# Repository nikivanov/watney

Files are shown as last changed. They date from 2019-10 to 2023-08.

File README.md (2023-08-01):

# Watney Rover
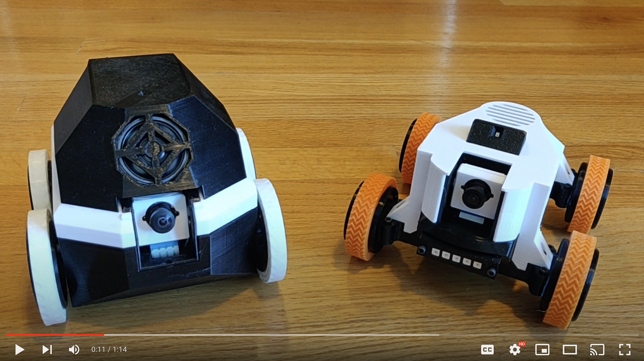
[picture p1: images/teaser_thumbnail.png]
(https://www.youtube.com/watch?v=ayU9SmKKkow)

Watney is an open source, Raspberry Pi-enabled telepresence rover made of readily available parts.
Non-electronic parts of Watney are 3D printable.
Watney provides a low-latency HD video feed as well as bi-directional audio with echo cancellation.
Watney uses a charging dock with passthrough charging for continuous operation.

If you've enjoyed this project and want to buy me a beer (no pressure): 

# Components
Head over to [Bill of Materials](BOM.md) for a list of components you need to purchase to build your own Watney. You'll also need a 3D printer, some PETG / Tough PLA as well as TPU filament. Lastly, you'll need a soldering iron and some wires, though most connections are made using standard breadboard jumper wire.

# UPS Firmware Update
Before you start assembling your Watney, be sure to update the firmware of the UPS power supply. At the time of writing, the latest firmware is *v10* - all previous firmware versions suffered from occasional lockups. You can find [firmware update instructions here.](https://wiki.52pi.com/index.php/EP-0136#Method_2)

# Printing the parts
You can find all 3D printable parts in the [STLs folder](https://github.com/nikivanov/watney/tree/master/STLs). I recommend printing everything but the tires in PETG (I used eSun PETG) or at least Tough PLA. I find regular PLA to be too brittle but YMMV. Print the tires in TPU - Hatchbox TPU worked great for me, but others will almost certainly work just as well.

Print every part with 0.2mm layer height. No supports are needed. The base part includes tearaway lilypads to help with adhesion. Generally, the prints can take a long time but none of them are particularly challenging to print.

# Assembly
You'll be working with Lithium Ion batteries - please be careful not to puncture or short them, as they can become a fire hazard if used improperly. **You assume all responsibility for damages that may be caused by your Watney, whether it's assembled correctly or otherwise.**

Click on the [Releases](https://github.com/nikivanov/watney/releases) tab and download the [latest Watney SD card image](https://github.com/nikivanov/watney/releases/latest) - it's the large .zip file found under *Assets*. Use [balenaEtcher](https://www.balena.io/etcher/) or similar to write the .img file onto the SD card.

After that, follow the detailed assembly video below!

Wiring diagrams that you see in the video can also be [found here](https://github.com/nikivanov/watney/tree/master/images/wiring).

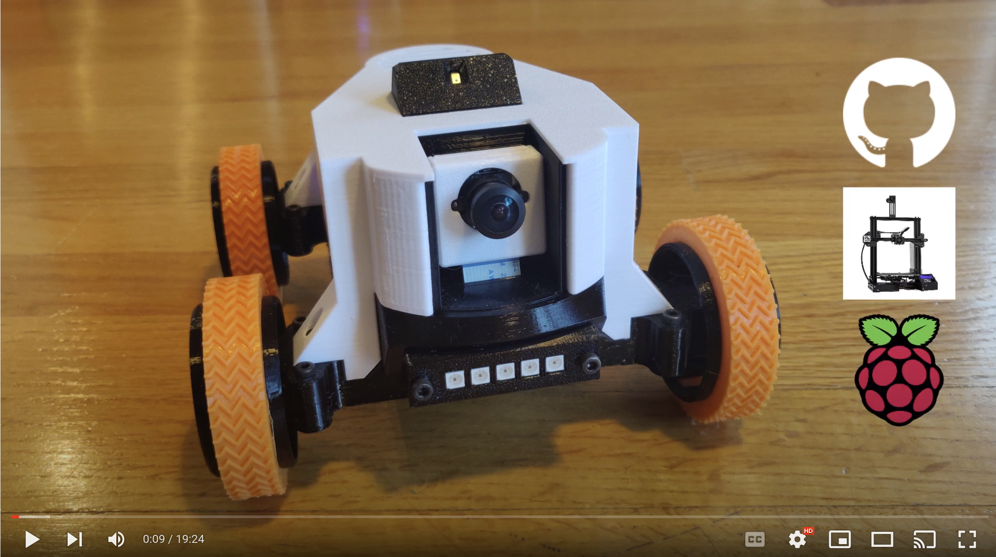
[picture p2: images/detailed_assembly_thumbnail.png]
(https://www.youtube.com/watch?v=wV26r6FtXRw)

 
# Configuration
Upon startup, Watney will detect if it's connected to a Wi-Fi hotspot. If not, it will host its own hotspot "Watney".
Once you connect to the hotspot, you can control it directly by going to https://192.168.4.1:5000, or connect it to a Wi-Fi
hotspot by going to http://192.168.4.1 Once you specify your WiFi credentials, Watney will take some time to reboot. Once you hear the startup sound, you're good to go!

Default SSH credentials for Watney are pi / watney5. Watney's mDNS name is watney.local, so if your OS supports mDNS you can simply access it at https://watney.local:5000

Watney's configuration can be found in ~/watney/rover.conf:
* If you want to use different GPIO pins, you can specify them here
* If you find motors on either side running in reverse (backwards when it's supposed to be rotating forward) simply swap ForwardPin 
and ReversePin
* Restart your Watney for configuration changes to take effect

    ## Off Charger re-docking
    Watney can detect when it is taken off the charger outside of its own movement and can attempt to re-dock by driving forward for one second. In my case, Watney occasionally gets knocked off the charger by my Roomba, so enabling this functionality ensures that Watney is always docked and charging. By default this functionality is disabled: I didn't want Watney to drive off someone's workbench while they are working on it. If you'd like to enable this functionality, set `Enabled=True` in the `OFFCHARGER` section of the config.
# Remote Access
Watney has no authentication / security. If you'd like to set it up for remote access, I recommend using [Zerotier](https://www.zerotier.com/). Adding Watney and your client computer to the same Zerotier network will make it appear as if they are on the same local network.

# Building your own Watney image
`packer-builder-arm` is used to build the Watney image. You can find the image build definition in [watney-image.json](packer/watney-image.json). [This article](https://linuxhit.com/build-a-raspberry-pi-image-packer-packer-builder-arm/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,server%20or%20other%20x86%20hardware.) may help setting up `packer` and `packer-builder-arm` on your linux system.

# Raspberry Pi Compatibility
Watney is designed to work with Raspberry Pi 3A+, however other versions may be compatible:
* [scifiguy000](https://github.com/scifiguy000) confirmed to have successfully used a Raspberry Pi 4B in [this thread](https://github.com/nikivanov/watney/issues/27)
* Raspberry Pi Zero 2 may work out of the box, but has not been confirmed yet

# Camera Module Compatibility
[camrichmond](https://github.com/camrichmond) discovered that the newest Raspberry Pi camera module v3 is not compatible with the current Watney image, since the camera module itself is not compatible with `raspivid`, which is how Watney gets
its hardware-encoded h264 video stream. New Bullseye RPi images use `libcamera` instead. The fix is to simply change the command in `video.sh` as detailed [in this comment](https://github.com/nikivanov/watney/issues/34#issuecomment-1646009610). Additionally, [camrichmond](https://github.com/camrichmond) modified the camera housing for the new camera module, which you can [download here](https://github.com/camrichmond/watney_Pi_CameraV3). Thanks [camrichmond](https://github.com/camrichmond)!

# Troubleshooting
* Watney works best with Chrome. Other browsers may not work well, or at all.
* Feel free to file an issue on GitHub if you have questions!

# Open Source Acknowledgements
The following open source projects were used in development of Watney:
* [Janus WebRTC Server](https://janus.conf.meetecho.com/)
* [GStreamer](https://gstreamer.freedesktop.org/)
* [Raspberry Pi Turnkey](https://github.com/schollz/raspberry-pi-turnkey) 

# Future Improvements
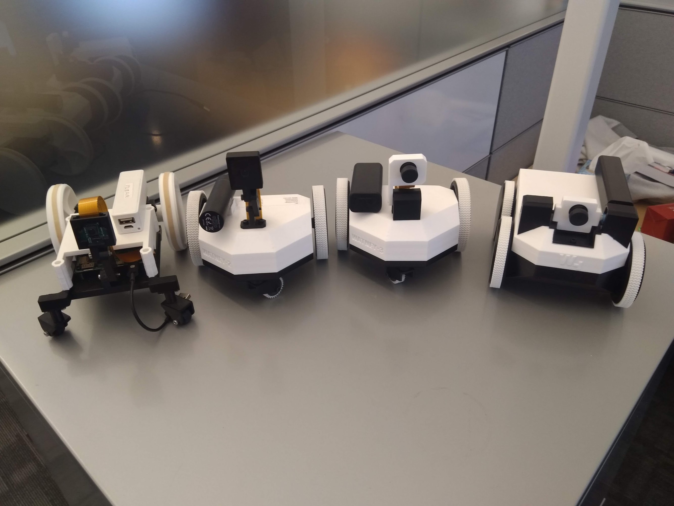
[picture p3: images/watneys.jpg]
Watneys

There have been numerous hardware iterations of Watney, starting from a humble line-follower built for a hackday work project, to the telepresence rover it is today. I'm not planning on adding new hardware iterations, as the latest version accomplishes everything I've envisioned for this project. That being said, there are still some software improvements to be made:
* **Mobile-optimized control.** You'll be able to control your watney from your phone / tablet, especially in tandem with Remote Access.
* **Better browser compatibility.** There's no reason it can't work in all major browsers.

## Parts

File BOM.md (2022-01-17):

# Bill of Materials
All parts can be found on Amazon, AliExpress, Ebay etc. Make sure the items you're ordering match the pictures. If you want to save money, order from AliExpress. Amazon will save you time on shipping, but will cost more. 

|Part| Reference Photo | Price | Notes |
|---|---|---|---|
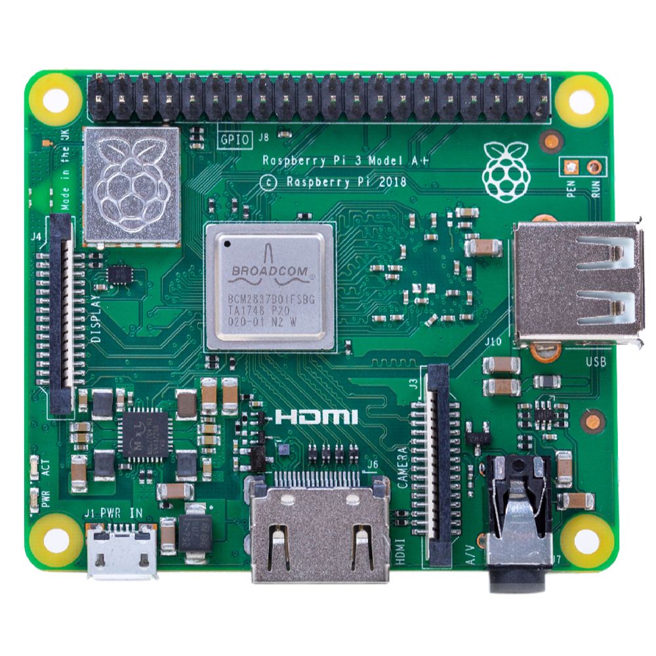
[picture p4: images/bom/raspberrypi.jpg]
raspberrypi
|Raspberry Pi 3A+|| $25 |
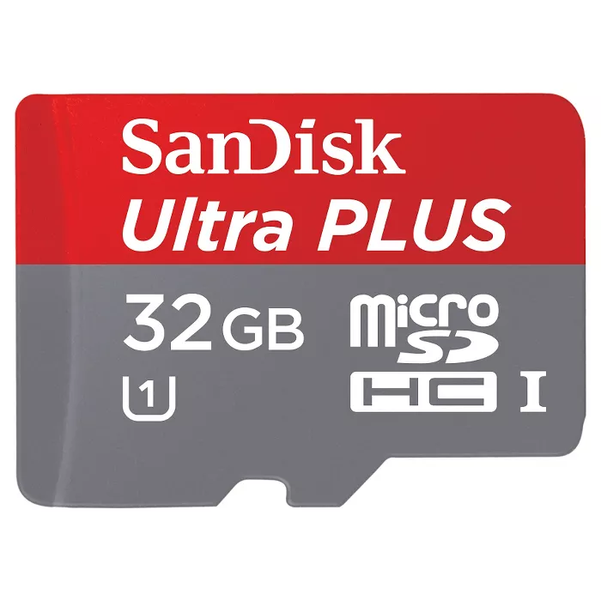
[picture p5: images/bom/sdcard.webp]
sdcard
| Micro SD Card 8GB+ | | $5 |
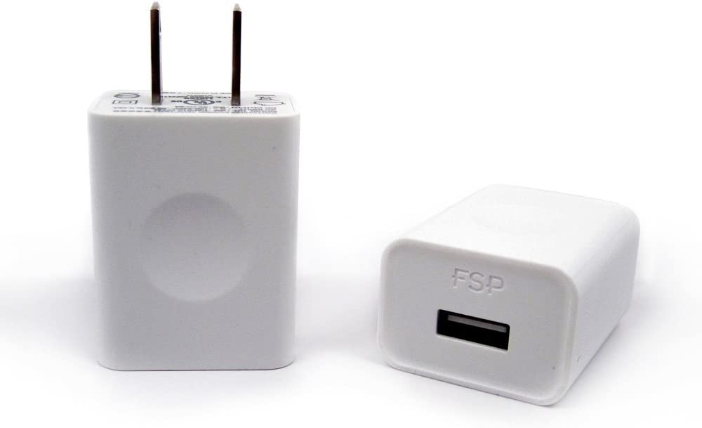
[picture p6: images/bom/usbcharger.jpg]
| 2A USB charger |  | $5 | 
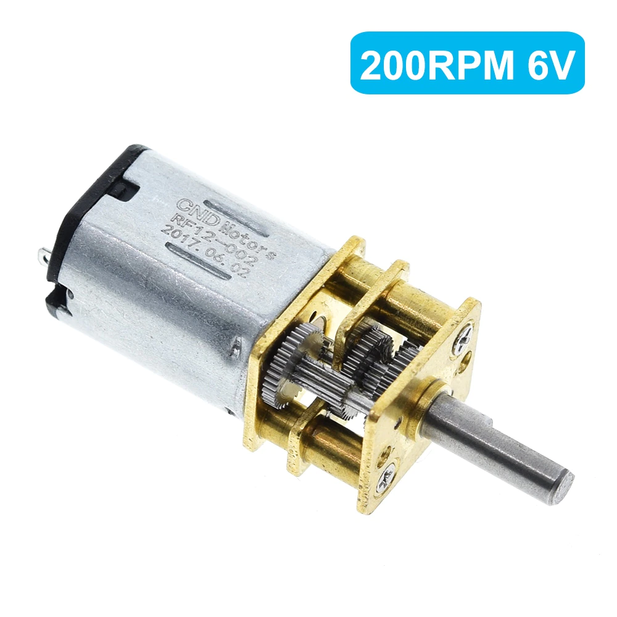
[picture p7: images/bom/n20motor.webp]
n20motor
| 4x N20 geared motors, 10mm shaft, 200 rpm, 6V | | $14 total | You can choose a lower speed to get more torque, but 200 rpm seems to have the best balance of torque to speed
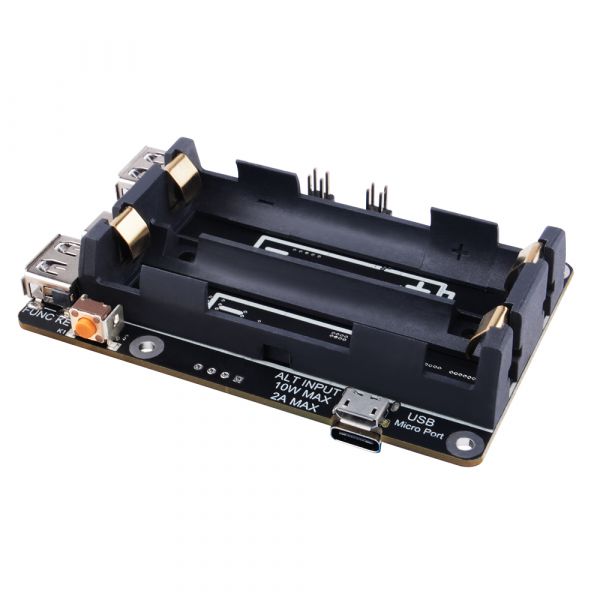
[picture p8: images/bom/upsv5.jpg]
upsv5
| GeeekPi UPS Plus V5 EP-0136  |  | $30 | Product Wiki: https://wiki.52pi.com/index.php/UPS_Plus_SKU:_EP-0136
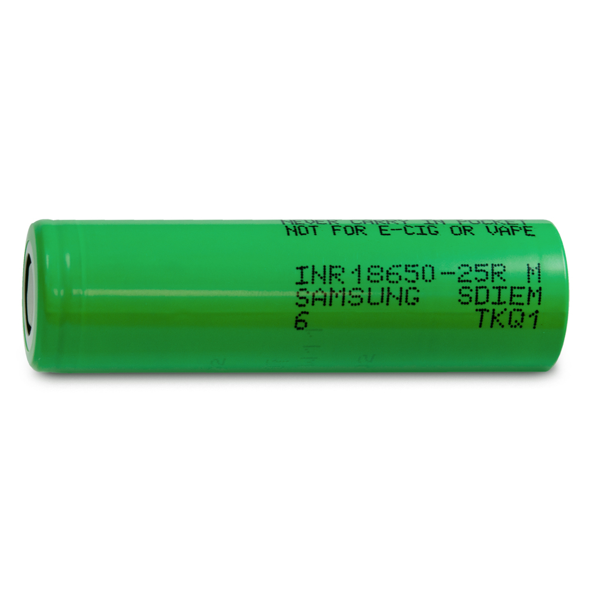
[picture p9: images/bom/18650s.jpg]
| 2x 18650 batteries | | $20 | The price is for 2 Samsung 25R batteries. You can save money by buying cheap 18650s with mixed results
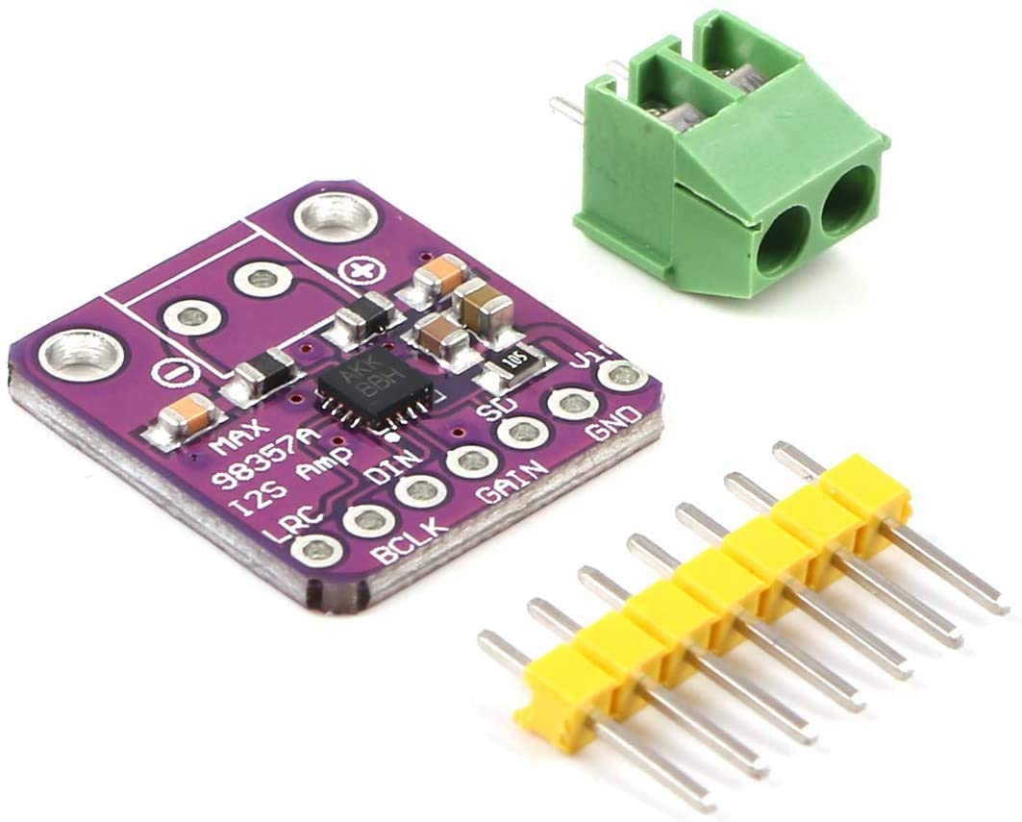
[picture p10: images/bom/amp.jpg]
amp
| MAX98357 I2S amplifier | | $4
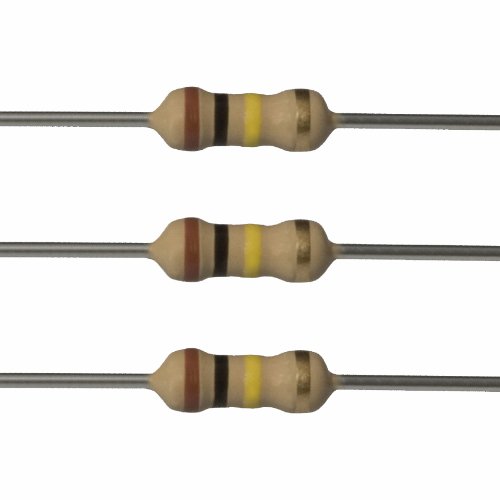
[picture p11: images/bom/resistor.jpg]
resistor
| 100k Ohm resistor | | $3 | Optional. Come in packs of 100 for the price 
| 40mm full range speaker |speaker | $5 | Usually come in packs of 2, but you only need one.
| Sipeed I2S microphone MSM261S4030H0 |microphone | $4 | Can be found under different names, but as long as it matches the image you should be good
| SG90 servo |servo | $4 | You may also be able to use the version with metal gears MG90. I haven't tried it but it should be a drop-in replacement
| Raspberry Pi fish eye camera | camera | $10
| DRV8833 motor driver |motordriver | $2
| 2.54mm 4 pin screw terminal |screwterminal | $3 | Usually come in pack of 10 for the price, but you only need 1
| SK9822 or APA102 144 LED/m strip |led | $20 | You only need a strip of 5 LEDs but the shortest strip you can get is 1 meter. You need the non-waterproof version, sometimes referred to as IP30
| 4x Keystone 209 contacts |keystone | $6
| Micro USB female breakout board |microusbfemale | $2 | This and the following USB boards usually come in a pack of 5 for the price
| 2x USB Type-A male breakout board |usbmale | $2 | 
| Micro USB male breakout plug |microusbmale | $2 | 
| 10cm and 20cm Female-to-Female Dupont jumper wire |  | $3
| M3 Bolt Hex Socket Round Cap 6mm 8mm 12mm 16mm 20mm |m3 | $6 
| 2.54m pitch male breakable pin header |header | $2 | You only need a few of these
| | | **Total**: ~$170 |

You'll also need general purpose hookup wire (in a pinch you can use jumper wire) and basic soldering equipment.

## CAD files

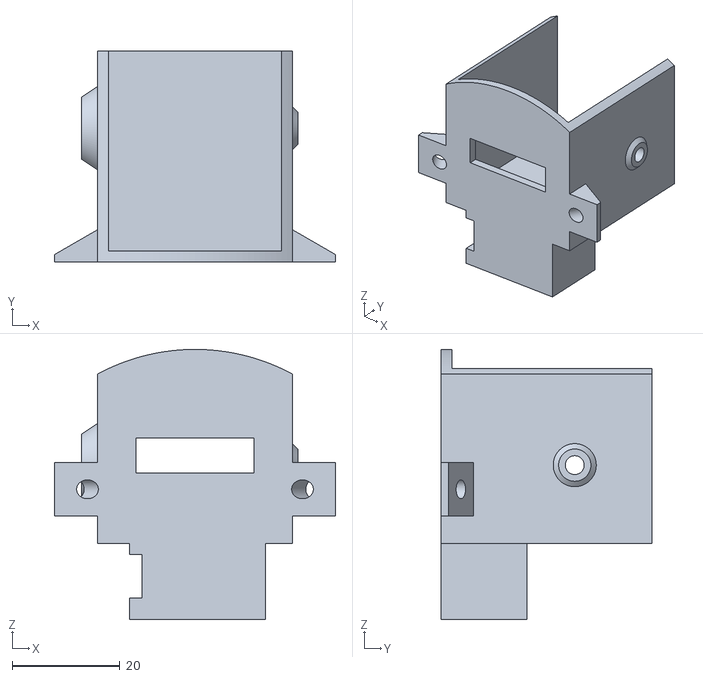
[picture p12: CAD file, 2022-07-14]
STLs/black parts/Camera bucket mg90s.stl
52.2 x 39.2 x 50.2

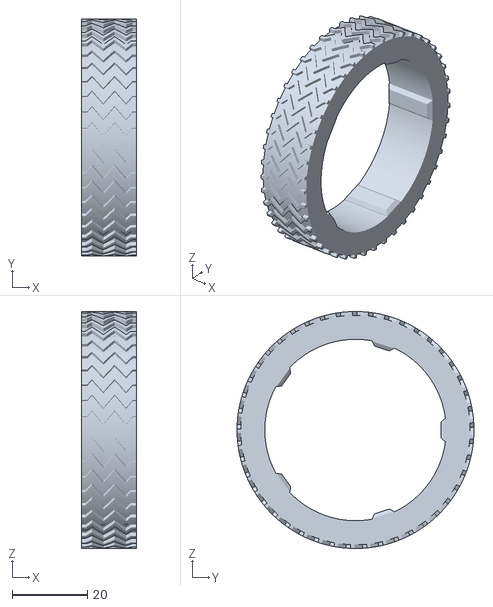
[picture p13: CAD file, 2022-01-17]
STLs/orange parts/tire.stl
14.5 x 63.0 x 63.0

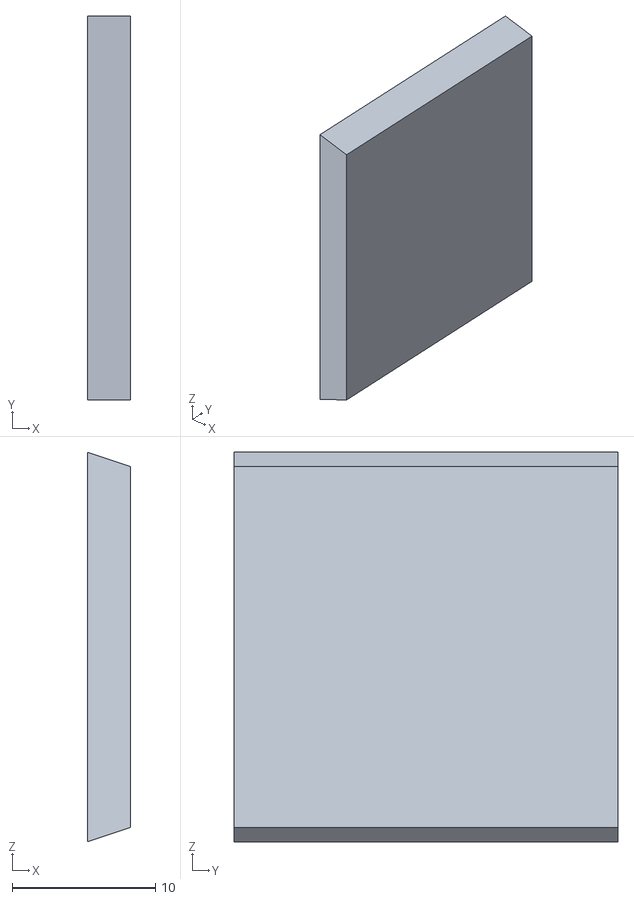
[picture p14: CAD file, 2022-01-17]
STLs/white parts/camera door.stl
3.00 x 26.8 x 27.2

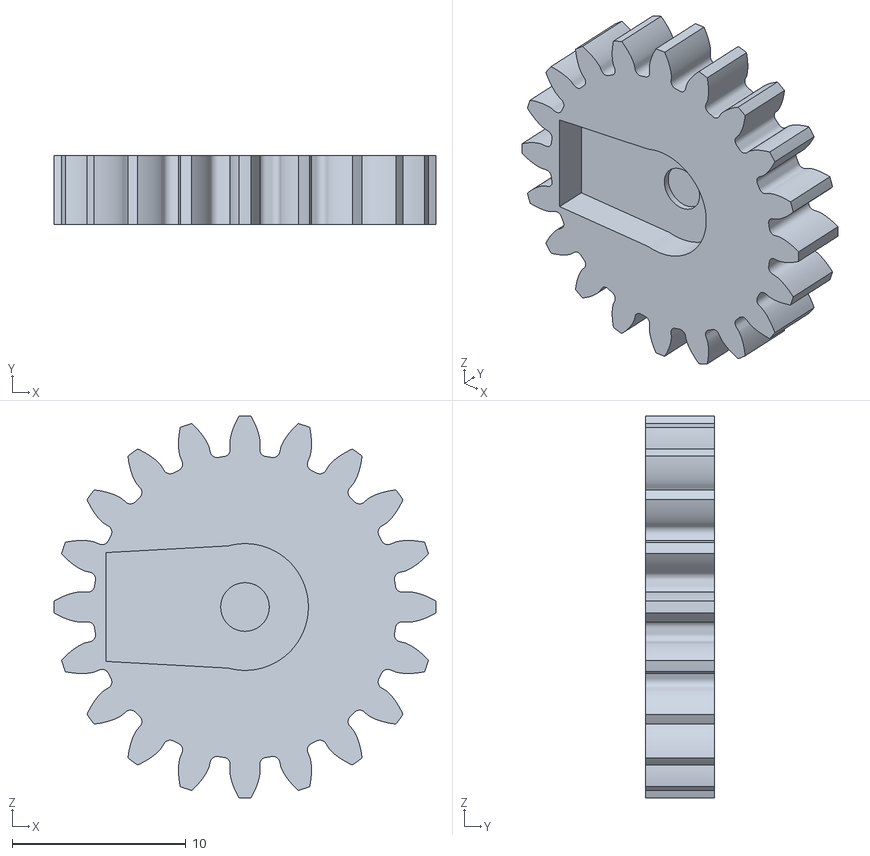
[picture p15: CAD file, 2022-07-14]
STLs/black parts/servo gear mg90s.stl
22.0 x 4.00 x 22.0

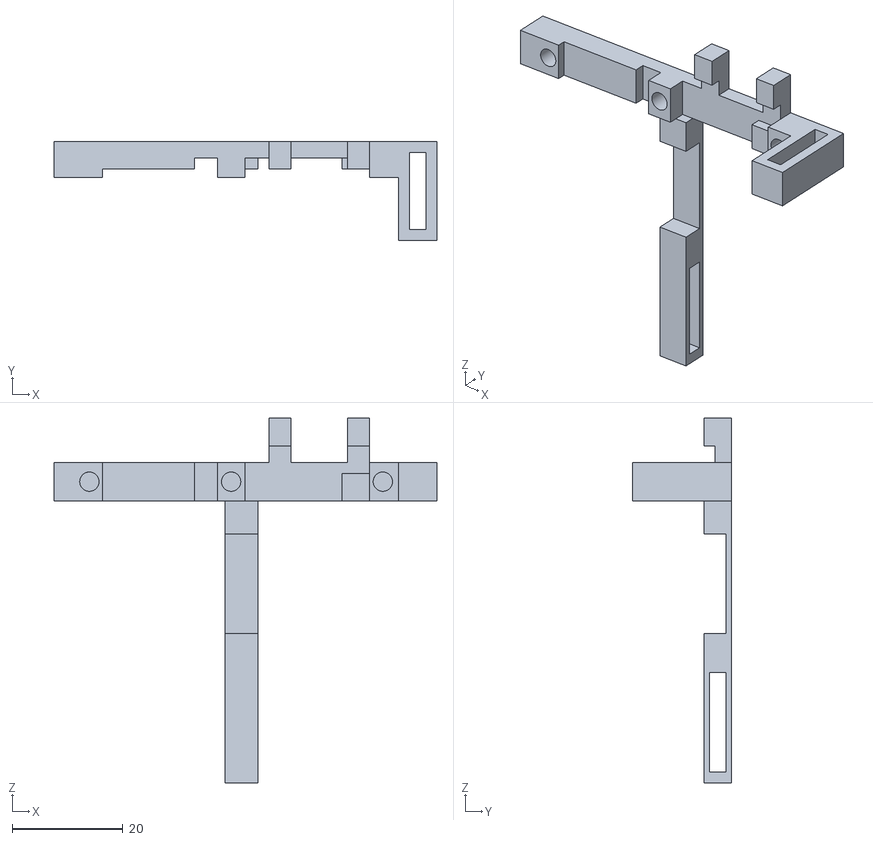
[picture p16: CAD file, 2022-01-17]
STLs/white parts/component clamp.stl
69.3 x 18.0 x 66.0

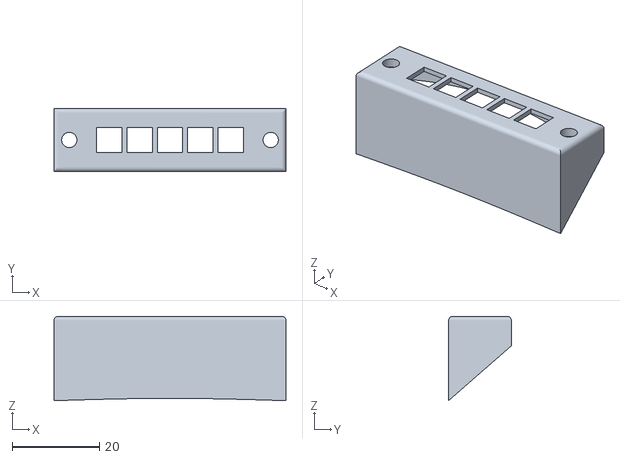
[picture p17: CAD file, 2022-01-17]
STLs/black parts/headlight case.stl
53.1 x 14.4 x 19.3

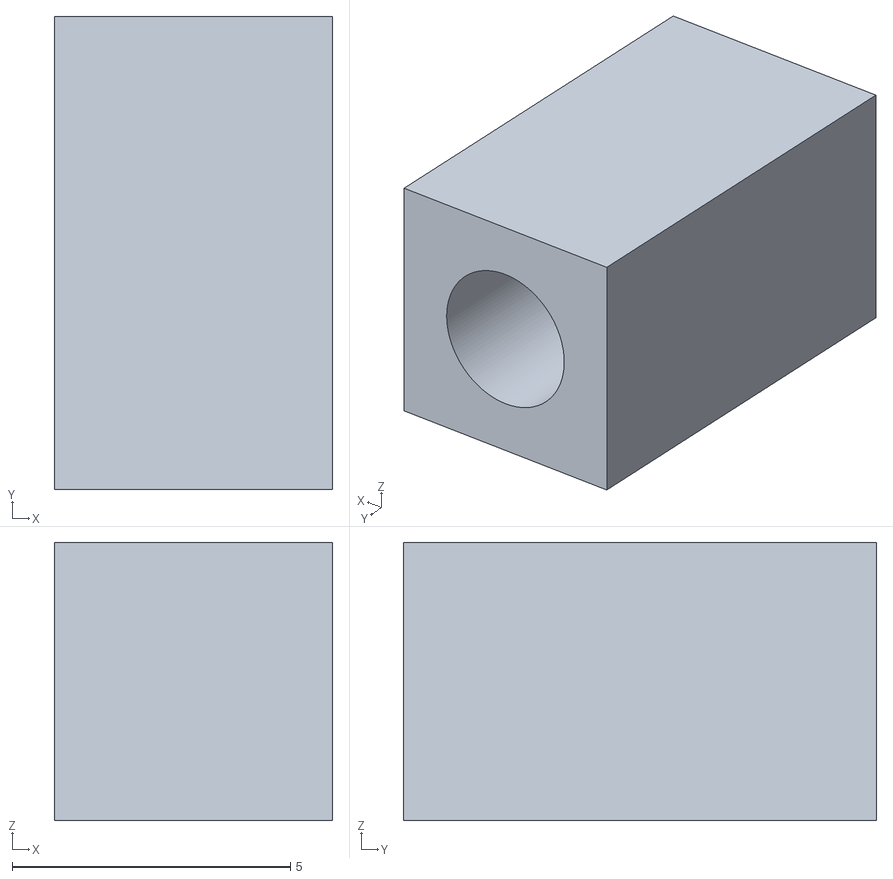
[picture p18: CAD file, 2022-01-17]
STLs/white parts/panel standoff.stl
5.00 x 8.50 x 5.00

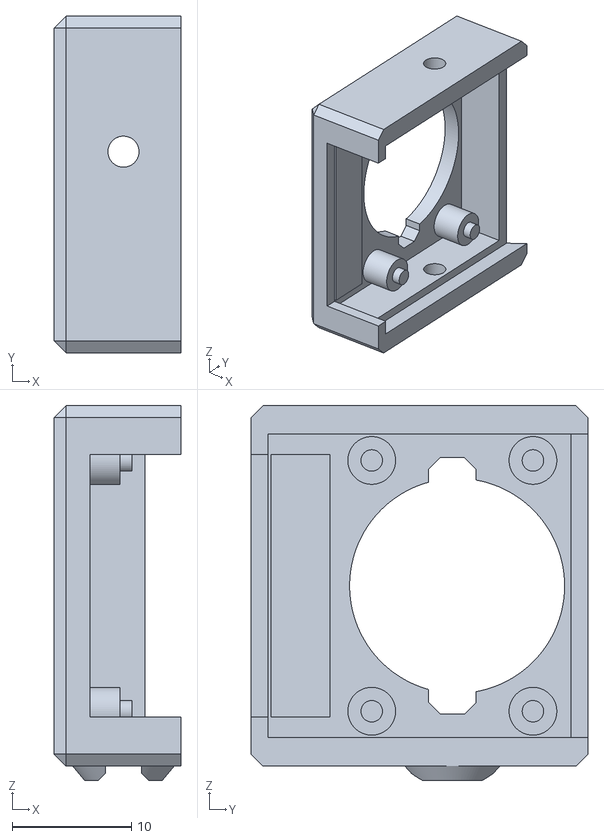
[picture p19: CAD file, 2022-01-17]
STLs/white parts/camera body.stl
10.6 x 28.2 x 31.4

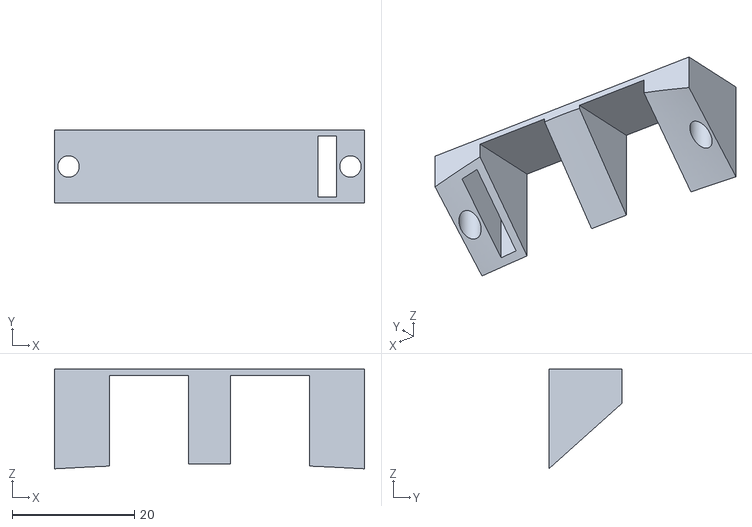
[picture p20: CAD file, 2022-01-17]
STLs/black parts/headlight mount.stl
50.7 x 12.0 x 16.3

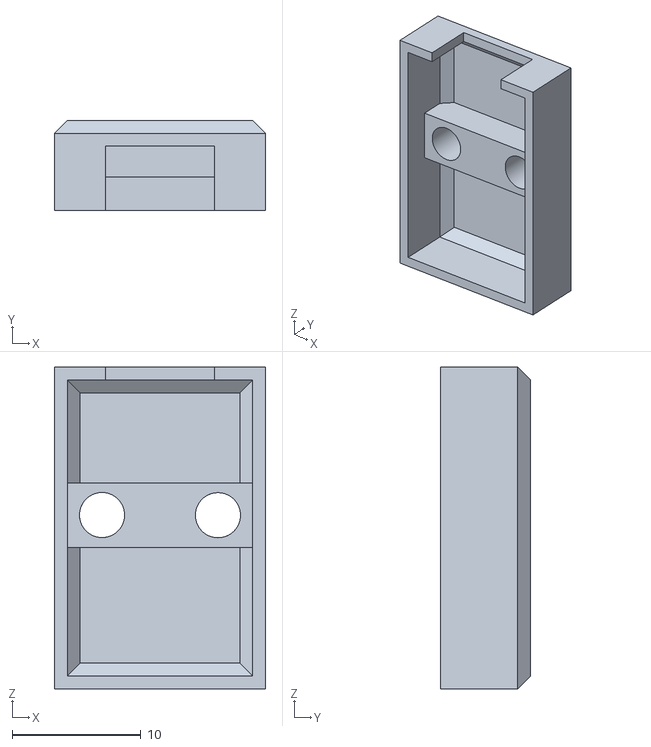
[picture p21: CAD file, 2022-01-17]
STLs/white parts/jack cover.stl
16.4 x 7.00 x 25.0

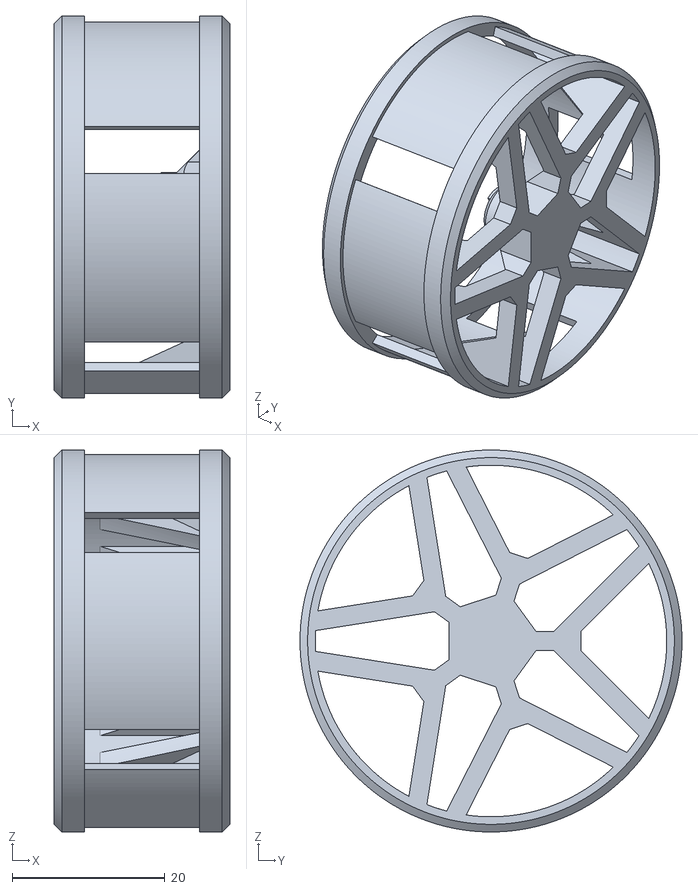
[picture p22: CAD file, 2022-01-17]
STLs/black parts/wheel.stl
23.0 x 50.0 x 50.0

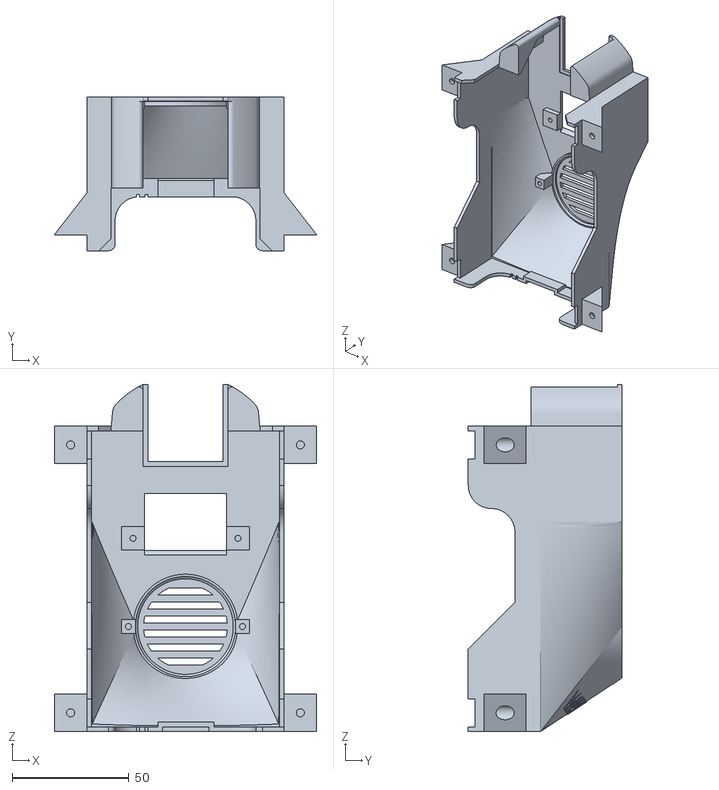
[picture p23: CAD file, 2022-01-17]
STLs/white parts/cover.stl
112.6 x 66.3 x 148.9

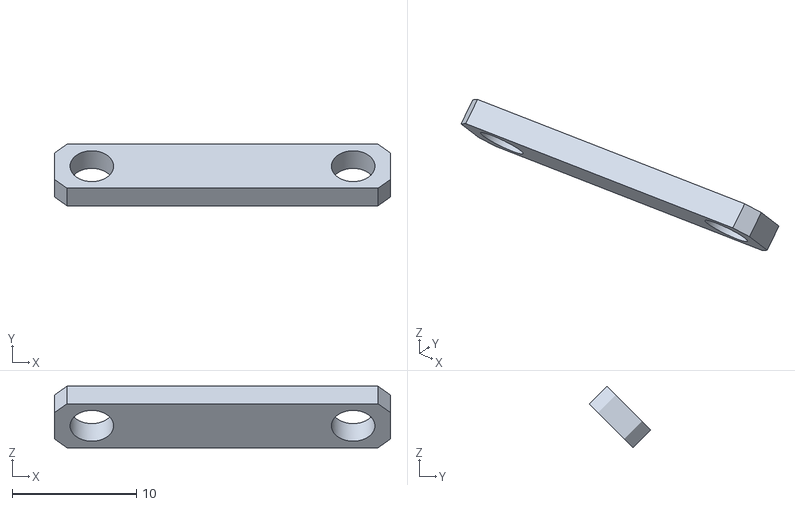
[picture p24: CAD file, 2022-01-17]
STLs/black parts/mic holder.stl
27.0 x 4.95 x 4.95

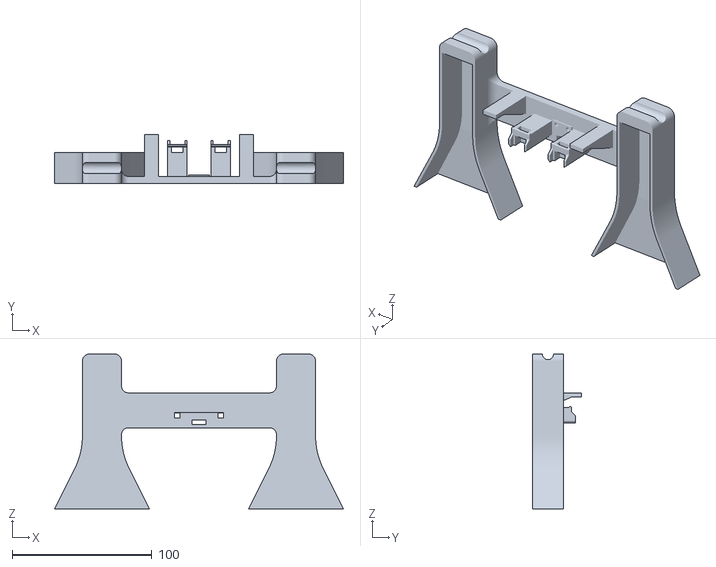
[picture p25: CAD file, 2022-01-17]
STLs/white parts/dock.stl
207.0 x 35.0 x 111.0

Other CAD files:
STLs/black parts/Camera bucket.stl
STLs/black parts/Power Button.stl
STLs/white parts/component panel.stl
STLs/black parts/Base.stl
STLs/black parts/camera gear.stl
STLs/black parts/contact board.stl
STLs/black parts/mic body.stl
STLs/black parts/motor holder.stl
STLs/black parts/servo gear.stl
STLs/white parts/speaker holder.stl

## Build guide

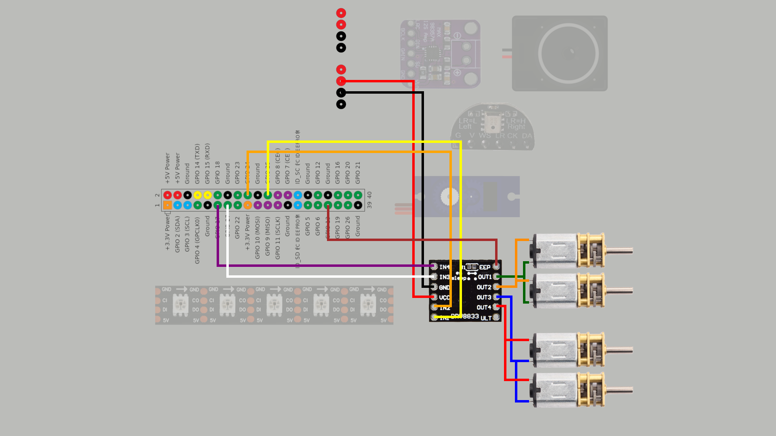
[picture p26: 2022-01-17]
images/wiring/motor wiring.png

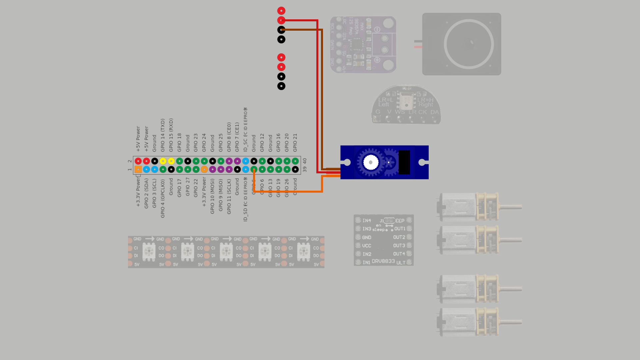
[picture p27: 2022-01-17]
images/wiring/servo wiring.png

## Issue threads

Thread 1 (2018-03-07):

LED lights

cyroassis, 2018-03-07:
Do you think it's possible to set a GPIO pin to turn on and off some LED headlights?

nikivanov, 2018-03-07:
I don't see why not. For simplicity, I powered the motor controller through Raspberry Pi's 5V pins. They are supposed to limit the current to 800mA. Using a cheap USB ammeter, I saw that the rover takes about 600-700mA while running at full speed, so you don't have a ton of wiggle room. Then again, if you stall the wheels, I saw consumption of up to 1.1A, which should have tripped RPI's 5V fuse. LEDs don't need much to run, so you should be ok.

Closed 2018-03-07.

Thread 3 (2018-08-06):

Great Idea

JasonTheDude, 2018-08-06:
I love this project!. The kids and I have had a great time printing it up and getting it all put together.
Is there a file or anyway I can get a simple ELI5 wiring diagram? Thanks I have the Ras Pi Zero

nikivanov, 2019-10-15:
The new version has detailed instructions on wiring

Closed 2019-10-15.

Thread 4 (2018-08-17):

Use a Raspberry Pi 3?

phrozen77, 2018-08-17:
Can you adapt this project to use a „normal“ Raspberry Pi 3?

jonaphin, 2018-08-20:
I was able to run it on a Raspberry Pi 1, it does require some fiddling with the image and OS setup. Nothing worked out of the box for me.

nikivanov, 2019-10-15:
The new version runs on Raspberry Pi 3A+

Closed 2019-10-15.

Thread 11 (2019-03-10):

Speech function?

farminguin, 2019-03-10:
Would it be possible to add eSpeak Text-To-Speech? Like a LM4871 audio amp ? Textbox on the web interface? Would be a great way to make it for of a telepresence bot. ..

svasiliou, 2019-03-24:
There is a 2way-audio branch but need explanation and wiring management.

nikivanov, 2019-04-08:
To get 2 way audio working, I had to switch to Arch Linux from Raspbian. The 2wayaudio branch isn't functional yet, so I'd avoid using it for now. Once it's ready, I'll release an SD card image along with BOM and 3d printed parts. Overall, the cost of adding 2 way audio is about $6 if you order from China (plus printed parts).

nikivanov, 2019-10-15:
2 way audio has been implemented

Closed 2019-10-15.

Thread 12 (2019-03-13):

Smartphone/Tablet control

svasiliou, 2019-03-13:
Project is awesome.
I believe that adding a few buttons (up/down/left/right/tilt) on lower  button row, would add functionality with tablet or smartphone. Is that possible or need complete redesign of code?

nikivanov, 2019-04-08:
Thanks! I'm currently working on adding 2 way audio so you can use Watney as a presence bot. After that I want to add wireless charging so it could be used indefinitely without needing to plug it in. For the latter part, I've been trying to figure out how to do voltage monitoring with Raspberry Pi - I'll look into the ADC you listed, thanks!

Adding a D-pad control for mobile interface has been on my list for a while, but I haven't gotten to it yet. Stay tuned!

svasiliou, 2019-04-08:
There are two interesting virtual joystick scripts
https://github.com/jeromeetienne/virtualjoystick.js (a little complex but more powerful)
https://github.com/cptx032/virtual-joystick (a simple one and I believe more suitable for WATNEY)

nikivanov, 2023-03-16:
@baheamri what would you like to know?

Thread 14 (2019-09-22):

No video

IgnacioHR, 2019-09-22:
Hello,

First of all, thank you for the material posted here. I'm having fun and learning a lot trying to build one Watney4

At this time, I've printed all parts and I've also modified some of them in order to adapt to the servo (GH-S43A) which is the only one I found that matches the required dimensions.

I'm still waiting for the motors for the wheels so I decided to test the other pieces separately from the entire robot.

The main problem I'm having is with the video. I've spent more than 4 days reading, compiling, changing things testing etc... with very little success.

1) I started using the software published on the "master" branch, but it looks like the video protocol is a security hole and not supported by browsers. So I realised I'd to go for the second branch (2wayaudio)

2) I moved to the new 2wayaudio branch. Downloaded janus from source (and several other libraries) tested if the video camera works and the scripts... and I'm stuck with a blank screen on my browser.

I'm still using a Raspberry pi zero W. It has no sound card so I can't test the sound. It might be good if sound is an option in the software so we could test things step by step.

Regarding the video. I've been able to save a sample video file in h264 format, upload the file to my MAC and then reproduce it on VLC so the hardware works and the first part of the video.sh script to capture the images from the capera works. OK.

I cannot test the second part of the pipe in the script. I've tried to use VLC on the Raspberry pi to implement the server side and test if the network is not a problem and I can see the video (with bad FPS...) but from time to time I can see images coming to VLC Client on the MAC.

But, when I start JANUS to test all pieces together, I'm stuck in a black screen with no images. The janus.log file says:

```[Sun Sep 22 23:49:37 2019] [WARN] [1962729996216110] No stream, queueing this trickle as it got here before the SDP...
[Sun Sep 22 23:49:37 2019] [1962729996216110] Creating ICE agent (ICE Full mode, controlled)
[Sun Sep 22 23:49:38 2019] [ERR] [sdp-utils.c:janus_sdp_get_codec_rtpmap:763] Unsupported codec 'none'
[Sun Sep 22 23:50:17 2019] [ERR] [dtls.c:janus_dtls_retry:1029] [2445920852038508] DTLS taking too much time for component 1 in stream 1...
[Sun Sep 22 23:50:17 2019] [janus.plugin.streaming-0xb2f08938] No WebRTC media anymore
[Sun Sep 22 23:50:17 2019] [2445920852038508] WebRTC resources freed; 0xb2f07108 0xb2f02ca0
[Sun Sep 22 23:50:17 2019] [ERR] [dtls.c:janus_dtls_retry:1029] [1962729996216110] DTLS taking too much time for component 1 in stream 1...
[Sun Sep 22 23:50:17 2019] [janus.plugin.videoroom-0xb2f051e8] No WebRTC media anymore; 0xb2f09e78 0xb2f06520
[Sun Sep 22 23:50:17 2019] [1962729996216110] WebRTC resources freed; 0xb2f09e78 0xb2f02ca0
[Sun Sep 22 23:50:17 2019] [WARN] [1962729996216110] No stream, queueing this trickle as it got here before the SDP...
```

and I don't know how to move forward...

Cheers
Ignacio

nikivanov, 2019-10-15:
Sorry I'm getting back to you so late.

I released a new version of Watney yesterday - this one definitely works, at least in Chrome. However, you need RPi 3A+, since Zero W doesn't have enough oomph to do both audio and video. Also I switched to a more popular SG90 servo.

Let me know if you're still trying to get the old Watney to work and I could help you troubleshoot it.

IgnacioHR, 2019-10-16:
Thank you for your response!

I do have some RPi 3A and 4 for testing and I will checkout the new version of the code and see where I can go.

Cheers
Ignacio

Closed 2020-04-23.

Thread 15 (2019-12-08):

When Backing off the Wireless Charger Watney will reboot instead of moving

rtaylo, 2019-12-08:
This little robot is amazing to drive around the house and I'm having a blast with it. The only issue I've found is that Watney will reboot when I attempt to back out of the wireless charging bay.  The result is that my rover is "stuck" on the charger without the ability to reverse.

For reference I am using:
https://www.aliexpress.com/item/32969639665.html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,searchweb201602_4,searchweb201603_55

Based on reviews it looks like it fails to work as a UPS.

rtaylo, 2019-12-09:
To resolve the issue I purchased this:
https://www.ebay.com/itm/352777629993

As it looks identical to what's pictured in the build guide.

nikivanov, 2019-12-23:
Yep, getting the EXACT board is essential. I'll update the README with a note of which board not to get. Thanks!

Closed 2019-12-09.

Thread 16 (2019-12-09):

Feature Request: LED Headlights

rtaylo, 2019-12-09:
I'm not sure where to put a feature request in, but I'd be happy to help work on this.
I think some bright LEDs in the front would be perfect for navigating dark spaces.

nikivanov, 2019-12-23:
You'd need to figure where to get power and how to toggle the LEDs.

For power, you have a spare 3V output on the power board and a 5V pin on the raspberry pi. You'd have to measure the current on both to find where you have more headroom. 5V would be easier, but it might already be pretty taxed. 3V is safer but more complicated when it comes to toggling.

For toggling LEDs on and off you could use a relay/mosfet, or use an individually-controlled LED strip, like WS2801 that would allow toggling natively. I think WS2801 is the easiest approach, as long as there's some headroom. The power board max output at 5V is 3A, but they recommend not going above 2.2A.

nikivanov, 2020-04-23:
I'm planning on adding headlights based on SK9822 LED strip. With 50mA per LED and 30/m strip, I think I can have 4 LEDs wrap around the front of Watney and provide enough illumination. Stay tuned! Closing this request for now.

Closed 2020-04-23.

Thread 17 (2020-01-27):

PID speed controller

dclause, 2020-01-27:
Hi !
I wondered if it would be interesting to setup a speed control within watney robot using this kind of motors :
https://www.dfrobot.com/product-1457.html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

The speed control could be done via the software or I wondered if this kind of card would fit in the robot if removing L298N (would not be necessary anymore in that case) :
http://www.dagurobot.com/Robot_Controller/Rover5_tank_motor_driver_board

Could you eventually advice me on this ?
I am wondering if driving straight while using FPV is easy or not without that kind of pid control.

nikivanov, 2020-01-28:
Hi!

Watney may not drive in the straight line if one of the sides spins faster than the other. There is rudimentary trim control in the config, which allows you to slow down one of the sides to compensate for it. This is a constant offset factor, so it won't work universally for all surfaces. What I usually do when driving a Watney is press and hold forward and adjust it manually by tapping left / right to compensate for it veering off course.

The motors you posted in the first link will give you feedback of how quickly they are turning. If you read all 4 motors' feedback, you can slow down one side if the other one is spinning slower in real time, which should give you better straight line driving. It still won't handle cases when one side is stuck with wheels spinning freely.

The board you posted should do all of this for you, though I've never tried using one like that. You can still use L298N, read the encoder data using the raspberry pi and adjust each side's speed accordingly. Note that since the motors are connected in parallel on each side, you can't control them individually, which would be optimal - you'd read all 4 encoders, determine the slowest motor, and adjust the other 3 to that speed.

Hope that helps!

dclause, 2020-01-29:
That helps a lot indeed ! Thanks a lot for your answer, and I am sorry for the lacks of my english in the rather long answer coming next.

I hope to build a robot that would be nice looking (ie not with no cables out everywhere), self battery charging, with a camera feedback to FPV-drive it, easy to maneouver, and small enough to navigate into ventilation duct (yep... that's a bit weird as a requirement !)

- I have built a custom bot over a dagu rover5 plateform that partially fits the need (currently running perfectly fine but running on arduino with a radio shield, would need to be turned to raspberry for wifi). Problem : the plateform is too big in essence.
- I have a custom bot inside a ZeroBot Pro chassis that works fine but is not able to go straight and the plateform is too small for including the wireless charger and more important : the motors' encoders and driver.

Hence, I think the shape of your platform has a perfect size. Plus I must say, the pieces prints perfectly, the "circles" under the pieces to help it sticking is a little detail that shows how well design they are. Well... kudos to you sir !

I have multiple hardware solutions that has been tested separately. I just can't get them fit all into one printable plateform. Each solution would need small adjustments, mainly in the places for the M3 screws. (for instance if replacing the L298N with the motor board I suggested in the bottom.stl).
The biggest change would be eventually if you had a mix between v1.3 and v2.0 cover.stl file : a cover that would fit the raspberry zero AND the audio bonnet in the same time.

Main reason for it : the raspberry A+ consumes 2.5x as much as the raspberry Zero while I don't require the extra computational power. And I would like to use that room for extra circuits :
- power switch (I could not find one in the current design)
- headlights (hence 2 resistors and a BC337)
- battery remaining charge reader (hence an ADC such as MCP3008 or ADC1115 which could also work as an encoder counter).

Your plateform is the closest I have found currently to my requirements but some details are different to your solution. Maybe this question is too much to ask, but *do you have original 3D files for share too so i could change it easily to my requirements ?*

I had write a very long solution describing multiple solutions :
- battery shield on the bottom plug directly to a type be wireless charger receiver (that would make the whole 'audio bonnet' useless in term of space.
- two L298N vs 4-motor driver board to benefit from the 4 wheel encoders
- software PID vs hardware PID
but after all, I think this was boring thoughts which all came down to the same : to test it, I always need some STL changes that I can't do.

In the software area, I already have it all (in nodeJS though) : the camera handling, the headlights, the encoders etc... the whole point is to drive the robot via FPV-google using a PC joystick so straight lines needs to be straight, otherwise the driving in the ducts is a nightmare.

I am rather close to my need : just being able to fit the hardware into something I can 3D print.

nikivanov, 2020-01-29:
Hi!

1. There is a power switch - it's the switch on the power board, accessible from the side on the audio bonnet. It cuts off all the power immediately, so it's not like a power button that you can handle in software.
2. If you want bidirectional audio, you have to use RPI 3A+. The reason I switched from Zero W is because it didn't have enough compute to encode / decode audio in addition to all the other stuff. WiFi is also a lot better on 3A+. On the other hand, if audio is not a requirement and WiFi strength isn't a concern, it should be easy enough to retrofit Watney to use Zero W again.
3. It's not too much to ask for original 3D files - in fact, they are already there! Under STLs, you can find watney.iges - you should be able to import it in a CAD software of your choice and mess around with it there.
4. Since you want to read battery voltage and have a dedicated encoder counter, you might as well add an Arduino Nano and slave it to the RPi. This would be a very cost effective solution. You can also have hardware PWM for motors and the camera servo that way.
5. There are many ways to accomplish what you're looking for with regards to going in straight lines. If your goal is to minimize changes, I'd do the following:

- Couple each side of motors with a toothed idler and a belt, like GT2. That should synchronize the rotational speed of each pair of motors. The current design should allow for this without modification of existing parts.
- Read one of the motor's encoders from each side and adjust each side's speed using PID or some other algo. You can probably keep all of the logic for that on Arduino and RPi will just issue high-level commands to it, like "forward 100%".

Please note that if you decide to do this, you'll need to open source your project as well.

dclause, 2020-01-29:
Thanks a lot for all those comments, you are awesome :)

1. I did not noticed ! At first sight I though the bonnet opening would be in front of the USB-type C port. I have not received the proper shield yet though, maybe that is why. I will double check as soon as received.
2. I don't need the audio indeed. But maybe that still would be more future-proof to go on with the A+. Any idea how long would the battery last with this ? (recommanded one at 3000mAh)
3. Many thanks. You can tell 3D is not my strength ! I did not know about this iges extension file. I need to learn more on this area :)
4. I though about the arduino nano solution indeed. To be honest, I thought that this would be an overkill solution. I guess I can generate the PWM from the raspberry itself using pigpio library. That may be not as effective as real hardware PWM, I have to test if running four motors and the servo with this technic, but that seems enough at first sight.
5. I like the belt idea :) that could be inner or outer if the wheels become a tank.

I will think more about it when I receive the required parts i will let you know. Regarding all changes (plus the fact everything is written in nodeJS), I guess the only remaining will be the 3D parts. I hope to come up with interesting feedbacks soon.

Thanks again.

nikivanov, 2020-01-31:
Happy to help!

In terms of battery life, I'm using Liitokala HG2 at 3000mah, and there's two of them in the battery pack, in parallel, totalling 6000mah. It gets boosted to 5V and there's some loss there. The main power suck are the motors, not the RPi. I've never done an extensive test, but I would assume that at the highest draw, you should be able to get 1 hr continuous - that's all motors are spinning at full speed with some resistance. I'm really curious to know if this is a good assumption.

I used to use pigpio but had to go back to RPi.GPIO because I didn't have any hardware interrupts - both PWM and PCM are taken up by audio / mic. If you aren't using audio, you can (and should) go back to pigpio. In my experience, hardware-timed PWM is pretty damn close to actual hardware PWM. It should suit your needs.

The geared motors have axles in both directions. I was toying with the idea of adding idles and belts inside the rover, but decided it adds unnecessary complexity and cost. If I were you, I'd try to keep the belts inside, but outside would work as well.

dclause, 2020-02-01:
Hi !

I receive the motors (see their 3D modeling here: https://github.com/Arduinolibrary/DFRobot_Micro_DC_Geared_Motor_with_Encoder/raw/master/FIT0450%20Solidworks%20File.zip).

Here are some thoughts on it :
1. The four motors don't fit on the rover. They are a little longer so that requires the bottom to be a little longer and the cover a little wider. I don't know how to transform the IGES file to something I can work on, I will try to learn that.
2. The dagu rover controller board will fit in the bottom part in place of the L298N. The screw holder though needs to be moved to fit the board size.
3. Electronics all works together and works with pigpio. I wrote the control in nodeJS and it works fine.
4. Your idea with the idler and belt would be good with one encoder-motor and a normal one on each side. unfortunately, the encoder-motor does not have a rotation tree on each side (only on the wheel side), so that solution won't work.

So here is the current state. I'm currently stuck with the 3D modeling. I need to learn more on that subject.

dclause, 2020-02-02:
Hello !
Okay, it took me quite some time to actualy learn a CAO tool. But it is funnny so that's cool !

I could not properly redifine the sizes from the IGES files (I did not succeed in turning the IGES file to something I could easily change. So I learn anyway to use the software therefore I rebuild it from scratch.

Here is the new bottom : it is a little longer so the four FIT0450 motors feats in.
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

I am now working on the cover. But I do have a question though about the purpose of the two small holes at the back as well as the rectangular one. Both circled on the following picture. Could you let me know what are they use for ?
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

nikivanov, 2020-02-02:
The ones at the top left give you visual access to the raspberry pi lights. The bottom right one can be used to pop open the case with a coin: besides securing the top and the bottom with screws, there are tabs that hold it by friction. Good luck with learning CAD - it's a worthwhile pursuit.

Closed 2020-04-23.

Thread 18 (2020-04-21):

Rover Access via DDNS

paalpwmd, 2020-04-21:
Hi @nikivanov ,

I am trying to set up the Watney for remote access, however,  I am having issues with requests to the Janus Server (hosted on port 8089).

I am wanting the access to be as easy as possible, with the video feed and controls embedded onto another site.

I've tried a few things so far:

Zerotier: Works well, but with the user restrictions I will run into the limit, plus it adds setup for the end user, which is not preferred.

I have forwarded ports 5000, 8088, 8089, 7088, and 53, and adding DDNS, hoping that would solve the problem. With this configuration, it doesn't change anything on the local network access. However, I am unable to access the video feed from the rover remotely. With the DDNS and port forwarding, I was still able to load the index.html, and the heartbeat requests are going through, so I'm getting the SSID, latency, quality, and CPU, and can also control the rover, but do not have access to the video feed.

However, in both of these circumstances, I am still getting the same errors. (See images below).
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

The best I can tell, these errors seem to be related to CORS headers. I have not found a way to configure those in Janus. Any advice or related information would be greatly appreciated.

nikivanov, 2020-04-21:
Hey Paal!

You may be better off asking someone on the Janus team. From what I remember, Janus also supports commands over websockets. You might want to enable websockets on the server and change how the javascript client connects to the server to use websockets. That should solve the CORS problem, but I've never tried it, so YMMV.

Please post your Watney on Thingiverse when you get a second - I love seeing them in the wild.

Nik

nikonowicz, 2020-04-21:
Hey Nik -

Thanks for the reply! Paal and I are working on this together. As an aside, I will drop an image of the build on Thingiverse today.

Looking at the errors we're receiving, it seems that maybe we just need to drop in some code that the CORS Preflight is looking for. I believe we understand what code it's looking for, but we aren't sure where it should go. We're also looking into websockets and some related questions with the Janus team per your recommendation. That being said, do you have any theories as to what 'requested source' within Watney it's referencing in the second screenshot when it says "No 'Access-Control-Allow-Origin' header is present on the requested source" ?

Regardless, thanks for building Watney! It's a blast to use.

Drew

nikivanov, 2020-04-21:
I think CORS is kicking in because Watney's interface is on port 5000 and Janus 8089. Going from localhost:5000 to localhost:8089 is considered cross-origin by your browser. I'm not strong on CORS, but I think you need to have both client and server to agree on allowing CORS. In my opinion, it'd be simpler to just switch to websockets for Janus API - the problem should go away on its own.

nikonowicz, 2020-04-21:
I see - we will look into it. If we find a coherent solution (with either CORS or websockets) I will loop back around to share it with you and anyone else interested in using Watney in this way.

Thanks for your time!

nikonowicz, 2020-04-23:
Thanks for the reminder - here it is! https://www.thingiverse.com/make:794163

nikivanov, 2020-04-23:
Thanks! Love the all-white

nikonowicz, 2020-04-26:
Hi @nikivanov -

Just a follow up. We were able to get this working. By updating the Janus configuration files to point to a TURN server that we hosted on EC2, we were able to allow users to communicate with the rover remotely using a DDNS. So the great news is that this is certainly possible, even if the Rover and Janus server are sitting behind a NAT. Just takes the right configuration.

As for CORS - in our case this error was appearing because of a bad port forward configuration. When we only forwarded the two ports necessary to themselves 5000:5000 and 8089:8089, this was fixed.

Thanks again for your replies before! Hopefully if anyone wants to do this in the future, this might help.

nikivanov, 2020-04-27:
Awesome! Please let me know when documentation is ready and I'll merge it into my repo as well. Cheers!

eerison, 2023-10-24:
Hey @nikonowicz thanks for sharing your results.

Could you list here what changes did you do and what tun server have you used please

Closed 2020-04-27.

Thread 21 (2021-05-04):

Possible to add servo for left right on camera

man4567890, 2021-05-04:
Hi,
Cool project, but I have a pan tilt servo mounted on the camera, where would the changes be in the code for using Q and W for left and right please, I connected the additional servo pin to GPIO3 and made changes in rover.conf
```
[SERVOUD]
PWMPin=2
# Min restricts the camera movement down
Min=5.5
# Max restricts the camera movement up
Max=9.2
Neutral=7.5

[SERVOLR]
PWMPin=3
# Min restricts the camera movement left
Min=5.5
# Max restricts the camera movement right
Max=9.2
Neutral=7.5
```
and added the new function to servocontroller.py

```
class ServoController:

    def __init__(self, config):
        Events.getInstance().janusFirstConnect.append(lambda: self.onJanusConnected())

        servoConfig = config["SERVOUD"]
        self.pwmPin = int(servoConfig["PWMPin"])
        self.neutral = float(servoConfig["Neutral"])
        self.min = float(servoConfig["Min"])
        self.max = float(servoConfig["Max"])

        servoConfig = config["SERVOLR"]
        self.pwmPin = int(servoConfig["PWMPin"])
        self.neutral = float(servoConfig["Neutral"])
        self.min = float(servoConfig["Min"])
        self.max = float(servoConfig["Max"])

```
But I do not know what changes are needed in the UI code, please

nikivanov, 2021-08-18:
Look in js/watney.js - you want to catch Q / W keyDown / keyUp, add lookLR near sendKeys and finally actually send it to sendCommand endpoint. In python you need to parse those values and call the servo controller

Closed 2021-11-30.

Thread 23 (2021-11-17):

Post your Watney builds here!

nikivanov, 2021-11-17:
Hi! Please post pictures of your Watney builds here.

rtaylo, 2022-02-01:
Video of Watney 2.0 with Flashlight attachment.

https://user-images.githubusercontent.com/21061419/152043389-0781231a-5ca4-4187-8e41-0215fb3ea45e.mp4

Syndesi, 2022-02-14:
Not a Watney robot, but similar in size and maybe an inspiration for a mod?
https://hackaday.com/2022/02/10/a-simple-3d-printed-rover-design
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
/

sarreck, 2022-03-14:
Just finished my build and its working really well.

Green is PETG, Yellow is ABS, black TPU for the tires.

Thanks for the great design
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

rtaylo, 2022-03-14:
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

Here's my garage. Open slot for new Watney 3.0

rtaylo, 2022-04-10:
https://user-images.githubusercontent.com/21061419/162643409-6dd32fcf-e642-4c96-9b4e-c07bddfb0bd7.mp4

rtaylo, 2022-04-10:
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

Spangen, 2022-12-08:
https://user-images.githubusercontent.com/4445078/206438544-97e8863e-fb91-4e12-a747-3627ae77e471.mp4

4 x hoverboard motors, 2 x reflashed hoverboard controller boards as motor drivers. 4 x 350W off torque from standstill and 4wd ;) I Put a chair on this thing, and sat on it. When I hit the trottle, I was thrown off ;)

Tried your new image to get to know webrtc and h264 streaming, and se how you solved audio. Is going to be great to ditch mjpeg-streamer on my 4G rover, it eats bandwidth ;)

Would be great with support for comute module 4, so we could use 2 cams. Reverse cam would be a great addon. Have that on another robot build I run on a modified Zerobot software setup.

Greatings from Norway

73 de LA5XOA

rtaylo, 2022-12-08:
Ha this is awesome

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

EGimagination, 2023-04-28:
This has been a Fantastic project, Thank you for sharing. Here is my Watney build, currently living within our local library that I volunteer at helping kids get into 3D printing and STEM learning.
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

fredmetal, 2023-12-08:
Nice Project, could the motor controllers be changed for L298N?

nikivanov, 2023-12-08:
> Nice Project, could the motor controllers be changed for L298N?

@fredmetal  I used L298N in previous versions of Watney, but it causes a fairly significant voltage drop. With 5V on the input, you lose quite a lot of torque due to the V drop, so I swapped it out for DRV8833. You can certainly go back to using L298N, but im not sure if there's enough space in the current design to accomodate for it.

fredmetal, 2023-12-08:
@nikivanov, I understand, I will continue with the DRV8833, thanks for sharing your project, crack!

nikivanov, 2023-12-08:
@fredmetal  Sure thing. Please open a separate issue if you have any questions or problems with assembly. Just a heads up - I'll be deleting this conversation from this thread in a bit - I'd like to keep it for build pictures only.

eerison, 2023-12-10:
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

Thank you for this nice project ♥️

nikivanov, 2023-12-11:
@eerison nice build! What kind of camera did you use? It looks like it doesn't quite fit into the housing.

eerison, 2023-12-11:
> @eerison nice build! What kind of camera did you use? It looks like it doesn't quite fit into the housing.

Hey nik

I am using this one

```
Bewinner Camera Module Board for Raspberry Pi B 3/2 2592 x 1944 Resolution 5MP High Resolution, Uses OV5647 Chip, Wide Angle of 175°
```

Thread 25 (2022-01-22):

Raspberry pi 4 compatible and STL file for the 4?

lyonrt, 2022-01-22:
Morning,

Is this compatible in with the raspberry 4?  Also do you have a 3d printer file for the 4?

nikivanov, 2022-01-25:
Hi. No, the current design is only compatible with rpi 3a+. It MAY be compatible with rpi zero 2, since it's pretty much the same thing as 3a+, but I havent tested it. I dont know what you mean by "Also do you have a 3d printer file for the 4" - if you're asking whether I have a CAD model of watney that works with rpi 4, I do not, sorry! If you end up making one, feel free to create a pull request!

Syndesi, 2022-01-27:
Hi,
would it be possible to publish the CAD-files for the current design, so that changes can be made faster than with the current STLs?
I also did see that you had [published the CAD-files for the previous design](https://github.com/nikivanov/watney/commit/674829ed6d9cad4c1d8d289af444f51b6bbcd62b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).
Regards, Syndesi

Akzotus, 2022-01-27:
I would also appreciate the CAD files for the current one if possible. There are minor changes here and there that make working on it significantly easier when given access to the editable files rather than dealing with the STLs.
The CAD files were immeasurably beneficial when working on the previous iteration.

nikivanov, 2022-01-27:
Theres a STEP file in the root of the STLs folder - it has everything you need

Akzotus, 2022-01-27:
Well I'll be darned.

nikivanov, 2022-01-31:
@Akzotus @Syndesi If you modify the existing version, please send me a picture of it! I'd love to see how people modify their Watneys. Please post it here: https://github.com/nikivanov/watney/issues/23

Closed 2022-01-28.

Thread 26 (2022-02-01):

Running new firmware on Watney 2.0?

rtaylo, 2022-02-01:
Is it possible to run the latest Watney build on Watney 2.0?
I have some SK9822 LEDs I ordered for my new Watney and I wanted to retrofit them on my older Watney 2.0

nikivanov, 2022-02-02:
Not without some work, unfortunately. First, the new watney I2S for both playback and recording. This frees up PWM hardware so I can use it for hardware-timed PWM, so things like servos and motors dont have jitter. Additionally, im pretty sure the code will crash if it can't talk to the new UPS over I2C. You can definitely make it work, but it'll require some effort.

Closed 2022-02-03.

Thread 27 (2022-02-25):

Running on Raspberry Pi 4B

scifiguy000, 2022-02-25:
Great project!  I've been having fun building it (it's quite an elegant design).  Many thanks to the originator(s) for their hard work!

I did some minor mechanical modifications and used a RPI 4B.  The image boots, and WiFi can be assigned at http://192.168.4.1.  After a reboot, I see it connected to my router, and I can SSH into it at its assigned IP address.  However, the web interface does not load, and the boot up Watney voice doesn't play.  I've verified the amplifier and speaker wiring, but since the web interface does not load, I suspect something more basic is going wrong.  Any ideas what to try?

Thanks.

--Mike

nikivanov, 2022-02-28:
Hey Mike! I already responded to you on thingiverse. After Watney starts up, ssh into it, type in "sudo systemctl status watney" and paste in the output here. If there are any errors on startup, you should be able to see them there. You can also stop the service "sudo systemctl stop watney" and then run it manually from ~/watney using "python3 server.py"

nikivanov, 2022-02-28:
Both 3A+ and 4B are ARMV8 architecture, but you might need to recompile for 4B. I used [packer-builder-arm](https://github.com/mkaczanowski/packer-builder-arm) and it lists:
```
raspberry-pi-3 (Archlinux ARM (armv8))
raspberry-pi-4 (Archlinux ARM (armv7), Ubuntu 20.04 LTS))
```

I'm not sure why RPI4 is armv7 there, it's armv8 last time I checked, but either way you might need to change that and rebuild

scifiguy000, 2022-02-28:
Ah, okay.  I'll try recompiling.

I answered on Thingiverse, but to keep this thread complete, here are some results:

pi@watney:~ $ sudo systemctl status watney
● watney.service - Watney Service
   Loaded: loaded (/etc/systemd/system/watney.service; enabled; vendor preset: enabled)
   Active: active (running) since Mon 2022-02-28 23:29:50 GMT; 14ms ago
 Main PID: 930 (python3)
    Tasks: 0 (limit: 3596)
   CGroup: /system.slice/watney.service
           └─930 /usr/bin/python3 -u /home/pi/watney/server.py

Feb 28 23:29:50 watney systemd[1]: Started Watney Service.

pi@watney:~ $ sudo systemctl stop watney
pi@watney:~ $ cd ~/watney
pi@watney:~/watney $ python3 server.py
Traceback (most recent call last):
  File "server.py", line 7, in <module>
    from lightscontroller import LightsController
  File "/home/pi/watney/lightscontroller.py", line 2, in <module>
    from apa102_pi.driver import apa102
  File "/usr/local/lib/python3.7/dist-packages/apa102_pi/driver/apa102.py", line 5, in <module>
    import board
  File "/usr/local/lib/python3.7/dist-packages/board.py", line 289, in <module>
    platform.system(), package[0], package[1]
NotImplementedError: Adafruit-PlatformDetect version 3.19.2 was unable to identify the board and/or microcontroller running the Linux platform. Please be sure you have the latest packages running: 'pip3 install --upgrade adafruit-blinka adafruit-platformdetect'
pi@watney:~/watney $

nikivanov, 2022-03-01:
Yeah that looks like an issue with a platform-specific build. You really just need to reinstall apa102-pi which I'm installing here: https://github.com/nikivanov/watney/blob/master/packer/watney-image.json#L86 . My guess is that when you install it, it compiles some code that's platform-specific.

I'm curious - where did you put the amp / motor controller if you're using RPI 4? Did you make standoffs / put them on top of the usb connectors?

scifiguy000, 2022-03-01:
I used the PCB carrier you designed, but cut off the center horizontal extension, and removed the standoff underneath.  I then used 3M foam tape to attach it to the top of the USB connectors, and bent the header pins to make them right angle (I could have used right angle pins from the start, but didn't think that far ahead).

I'm learning how to use Packer Builder, and it's slow going.  I also have shoulder surgery tomorrow, so expect some delay before I have results to report.  Once I get it to run properly, I'll assemble it and post pictures.

nikivanov, 2022-03-01:
Good luck with your surgery! When you're back, check out this: https://linuxhit.com/build-a-raspberry-pi-image-packer-packer-builder-arm/ I used it as a guide for building watney's image using packer.

scifiguy000, 2022-03-08:
I'm back, mostly recovered from my surgery (biceps tenodesis, with some additional shoulder work).  Now that I can use both arms, I got Watney working with the Pi4.  You were right, nikivanov, all it took was "pip3 install -I aiohttp apa102-pi psutil pyalsaaudio smbus" from a shell, and Watney booted up and played the voice message.  I'll do the final assembly, and post pictures.  Thank you!

nikivanov, 2022-03-12:
Hey Mike,

Glad to hear your surgery went well. Thanks for confirming how to get Watney to work with RPI4. I'll close this issue and update the main README page with a link to this thread.

Nik

scifiguy000, 2022-03-15:
It appears I spoke too soon.  I got excited because the boot voice and streamer worked, but it seems that's all that is working.  Motors don't run, and headlights don't turn on.

pi@watney:~ $ sudo systemctl status watney
● watney.service - Watney Service
   Loaded: loaded (/etc/systemd/system/watney.service; enabled; vendor preset: e
   Active: active (running) since Tue 2022-03-15 22:09:38 GMT; 5min ago
 Main PID: 651 (python3)
    Tasks: 43 (limit: 3596)
   CGroup: /system.slice/watney.service
           ├─651 /usr/bin/python3 -u /home/pi/watney/server.py
           ├─660 /bin/sh -c /opt/janus/bin/janus -F /opt/janus/etc/janus/
           └─661 /opt/janus/bin/janus -F /opt/janus/etc/janus/

Mar 15 22:09:45 watney python3[651]: Saying 'Watney... Online'
Mar 15 22:09:49 watney python3[651]: New janus session 7139316904631356
Mar 15 22:09:49 watney python3[651]: Firing Session Started event
Mar 15 22:09:49 watney python3[651]: Executing '/home/pi/watney/video.sh'
Mar 15 22:09:49 watney python3[651]: Logging to '/home/pi/watney/video.log'
Mar 15 22:09:49 watney python3[651]: Starting audio pipeline
Mar 15 22:09:49 watney python3[651]: Audio pipeline started
Mar 15 22:09:50 watney python3[651]: Removed Janus session 7139316904631356
Mar 15 22:09:50 watney python3[651]: Firing Session Ended event
Mar 15 22:09:50 watney python3[651]: Stopping audio pipeline

nikivanov, 2022-03-16:
Let's try to diagnose motors first: `sudo systemctl status pigpiod` - might make sense to restart watney and do it soon after bootup, so the logs don't get rotated. The service should be up and running. Does the camera move up and down? Both the motors and the camera are driven by PWM, so if one works but the other doesnt pigpio is not the culprit.

scifiguy000, 2022-03-16:
Thanks, nikivanov.  I really appreciate your help.

The camera does move when I use the web interface to control it.

pi@watney:~ $ sudo systemctl status pigpiod
● pigpiod.service - Daemon required to control GPIO pins via pigpio
   Loaded: loaded (/lib/systemd/system/pigpiod.service; enabled; vendor preset:
   Active: active (running) since Tue 2022-03-15 22:17:20 GMT; 18h ago
  Process: 388 ExecStart=/usr/bin/pigpiod -l -t 0 (code=exited, status=0/SUCCESS
 Main PID: 405 (pigpiod)
    Tasks: 6 (limit: 3596)
   CGroup: /system.slice/pigpiod.service
           └─405 /usr/bin/pigpiod -l -t 0

Mar 15 22:17:20 watney systemd[1]: Starting Daemon required to control GPIO pins
Mar 15 22:17:20 watney systemd[1]: Started Daemon required to control GPIO pins
lines 1-11/11 (END)

nikivanov, 2022-03-17:
If the camera moves that means pigpiod can generate PWM correctly. Please check your wiring: make sure your Vin / Gnd are not reversed on the motor controller (it should have a red LED on when it's plugged in). Also check the GPIO pins, but if NO motors spin at all whether you press up or down, then it's probably a power issue. I'd also make sure you have 5V on the USB pins into which you're plugging in your motor controller. Finally, just make sure that the jumper wires aren't broken. Basically get your multimeter out and start poking :)

scifiguy000, 2022-03-17:
I had previously verified correct power and polarity to everything with a DVM, but I just discovered 2 issues with the wiring:

On a hunch, I swapped data and clock on the LED strip, and it started working.  The connections are correct to the Pi4, but it appears "D1" and "C1" on my bargain AP102 LED strip from a Tindie seller are mislabeled.

The problem with the drive motors was a bad jumper on EEP.  I swapped with another one, and it works.  I'm guessing I'd probably find a pin is crimped to insulation instead of wire.

All is working now.  Sorry for unnecessarily reopening an issue.

Thank you!

nikivanov, 2022-03-17:
No worries, glad you got there. I'll keep it open for now - please confirm once everything is working and I'll close it

scifiguy000, 2022-03-17:
I have everything working, except the I2S microphone.  I was unable to get the brand in the BOM, unless I wanted to wait for a shipment from China, so I used the Adafruit I2S mic (https://www.adafruit.com/product/3421), and wired it accordingly.  Should the Watney mic be always on, or does it have to be enabled somehow?

nikivanov, 2022-03-18:
The mic is never enabled or disabled - it's more like whether RPi is running code to collect the data from it or not. If you open Watney's page and the video stream starts playing, you should also have the audio from the mic. Adafruit I2S mic should work - I actually used it in the previous version of Watney. The problem with it is that sometimes it produces white noise instead of normal recording. I never figured out why. I think it may have to do with the 3V line on RPi but I never confirmed it.

One thing I'd check is the channel selection on the mic. As you can see here in the video https://youtu.be/wV26r6FtXRw?t=969 LR pin of the microphone is connected to 3V and the microphone itself says "LR=H - Right" meaning if LR pin is high, then it'll use the right channel. You can also find the amp documentation (https://learn.adafruit.com/adafruit-max98357-i2s-class-d-mono-amp/pinouts) that says "If the voltage on SD is higher than 1.4V then the output is the Left channel." The mic and the amp are both I2S devices sharing one I2S bus of the Raspberry Pi. I use the Right I2S channel for recording and Left I2S channel for playback. If you're using a different mic, make sure that that mic is also set to Right channel only.

Looking at your mic's documentation (https://learn.adafruit.com/adafruit-i2s-mems-microphone-breakout/pinouts) it seems SEL pin also has to be set High for it to use the Right channel.

Hope that helps!

nikivanov, 2022-03-22:
Oh and another thing - you can easily test the mic by using `testrecord.sh` found in ~/watney : https://github.com/nikivanov/watney/blob/master/testrecord.sh

It'll record from the mic and save it to test.ogg in that same folder. You can use testplayback.sh to play it on Watney itself as long as the amp is working and the volume is up. Otherwise you can download it to your computer and play it there.

nikivanov, 2022-06-29:
Closing due to inactivity. @scifiguy000 let me know if you're still having trouble with it

nicolasbeni41, 2024-03-06:
Hello my raspberry pi 3a+ does not boot with the IMG provided but with a normal raspbian distribution yes what should I do?

4 green flash + 7 green flash

start*.elf not found
Kernel image (kernel.img) not found

Closed 2022-06-29.

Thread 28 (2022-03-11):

Dock missing from Watney 2.0 STLs

rtaylo, 2022-03-11:
would you be able to post the dock STL for the 2.0 version of Watney? I have to reprint it.
(I'm also waiting on some part to build my 3.0 version, can't wait!)

nikivanov, 2022-03-12:
Oh wow, I never noticed that the dock was missing. I'll upload it in a few days and link you to it.

rtaylo, 2022-03-13:
Awesome! Thanks. I just needed to reprint it and modify it some. I'm using
a different wireless charger and need a bit more space underneath.

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

nikivanov, 2022-03-13:
Hey @rtaylo I've uploaded the missing dock files. Since you're going to be modifying the dock, I figured you might want the STEP file, so here are both the STL and STEP files for the dock:

https://github.com/nikivanov/watney/blob/watney2_0_dock/STLs/dock.stl
https://github.com/nikivanov/watney/blob/watney2_0_dock/STLs/dock%20v11.step

rtaylo, 2022-03-13:
Awesome! Thanks mate. I need to post a picture as well of my Watney garage.

(Building my 3.0 soon)

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

Closed 2022-03-13.

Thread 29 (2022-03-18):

Watney 2.0 Constant Reboot While on Wireless Charger

rtaylo, 2022-03-18:
Hi Nikivanov,

Have you ever encountered an issue where Watney 2.0 reboots while connected to the wireless charger?
I'm thinking about retrofitting the Watney 2.0 with the new charging contacts.

Thanks

nikivanov, 2022-03-19:
Yes, this is one of the reasons for the redesign of Watney 3.0. The UPS used in 2.0 used to work as a true UPS in an older hardware revision. It also had 3 5V outputs and 3 3V outputs. It was also cheap to boot. It was perfect. However, the hardware was revised and the new revision does not function as a true UPS: when you supply 5V power to the UPS, the power to the devices would get cut off for about 200ms or so.

rtaylo, 2022-03-19:
I actually managed to get around the UPS issue by putting Watney on a wifi
smart plug. This allowed me to remotely turn on/off the plug. But my motors
arrived today for the Watney 3.0 build. Thanks for the input sir! Can't
wait to build the new version

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

nikivanov, 2022-03-20:
Good luck! Let me know how it goes.

Closed 2022-03-20.

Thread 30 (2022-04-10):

Feature request: Additional servo control

sarreck, 2022-04-10:
Hi,

Thank you for the great project.

It would be really useful if there was an additional preconfigured servo PIN to allow additional functionality (e.g. left/right camera, turret or RC LED control).

There would also need to be associated keyboard keys for the web UI.

In my case I want to control a RC car type LED which is controlled as a servo (works fine when connected to the camera servo in testing)

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

Thank you for considering this.

nikivanov, 2022-04-11:
Hi! To confirm, it sounds like you want another servo control bound to a new pair of keys. Is that correct?

nikivanov, 2022-04-11:
Do you know how to code? I can point you to a few files that you'd need to modify to make this happen.

sarreck, 2022-04-13:
> Hi! To confirm, it sounds like you want another servo control bound to a new pair of keys. Is that correct?

Yes thats correct.

sarreck, 2022-04-13:
> Do you know how to code? I can point you to a few files that you'd need to modify to make this happen.

I have tried based on your response to an older issue, however I was not able to get it to work as I didn't really know what I was doing.

nikivanov, 2022-04-13:
It shouldnt be difficult. I'll create a new branch and you should be able to copy the new files. I'll let you know when it's ready for you to test.

sarreck, 2022-04-13:
Thank you, I appreciate it.

nikivanov, 2022-04-20:
Hey @sarreck! I've made a new branch for your auxiliary servo. You can find here it: https://github.com/nikivanov/watney/tree/auxservo

By default the aux servo is on pin 6 and up/down is D / C

sarreck, 2022-04-23:
Thanks, that works great!

Closed 2022-04-23.

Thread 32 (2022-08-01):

Watney Microphone Loud Static, No sound

rtaylo, 2022-08-01:
I ordered a replacement mic module thinking that was the issue. But even after swapping the micrphone and double checking my wiring  all I'm hearing on the Watney web interface is loud static. Any suggestions?

nikivanov, 2022-08-03:
Hey @rtaylo ! I've seen this happen a few times while I was developing Watney. There are a few suspects:
- Are you using the recommended microphone - the one matching the picture from BOM? Or are you using SPH0645? I've had nothing but issues with the latter, which is why I switched to the current one.
- If you are using the mic from BOM, make sure the wiring is correct when it comes to L/R selection - the microphone LR pin should be connected to a 3.3V pin on Raspberry pi, which forces it to use the left channel. At the same time, the amp's SD pin should be connected according to [the diagram](https://github.com/nikivanov/watney/blob/master/images/wiring/audio%20wiring.png) - this will force the amp to receive on the right channel. If either get crossed up, you'll get static
- One of my microphone boards simply did not produce anything but static. I chucked it, since doing a drop in replacement with another board solved the issue
- If nothing else works, do a test in isolation - install plain raspbian on your raspberry pi, hook up just the microphone and try recording

rtaylo, 2022-08-04:
Here is the microphone I purchased.
I printed out the wiring diagram and followed it closely. Does this seem
like the right microphone?

https://m.aliexpress.com/item/2251832824703750.html?spm=a2g0n.order_detail.0.0.32cef19cur1lzU

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

nikivanov, 2022-08-04:
That looks to be the right microphone. I suggest you install vanilla raspbian on your RPI and make sure the mic works OK in that environment.

rtaylo, 2022-08-09:
Good thinking, I will do that and report back

nurglexp, 2022-10-15:
I have exact same issue with https://www.aliexpress.com/item/4001244371729.html

Do you have a link to a known working microphone?

rtaylo, 2022-10-15:
I still haven't been able to get this working

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

nikivanov, 2022-10-20:
Hi @nurglexp and @rtaylo. @nurglexp this is the correct microphone. Generally, when I buy parts from aliexpress I buy a bunch, 3-5 depending on the price. Usually they are cheap enough that I'd rather pay a bit more money than order one, wait a month, get a part that's potentially broken and then have to order again. I ordered 5 of these microphones and had this exact issue with one of them. To be fair, I had this same issue but more intermittent with the Adafruit I2S microphone that I used in the previous version of Watney. However, with these mics my experience has been that they either always work or never.

My advice is to buy 1-2 more of the microphones, preferably from a different supplier, and see if you can resolve the issue by simply replacing the part.

Another thing you can try is to disconnect everything but the microphone from the raspberry pi, leave it unpowered for a few hours (more on that later), start it up, SSH into watney and run [this script](https://github.com/nikivanov/watney/blob/master/testrecord.sh) It will record from the mic into `test.ogg` file. Transfer it to your PC and see if it's noise, silence, or actual sound recording.

Let me know how that goes for you!

rtaylo, 2022-10-20:
Will do, thanks Nik! I've actually got a new baby and I'm about to start
heading back into the office. I'll be using Watney to spend time with the
wife and baby while I'm at work lol

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

nikivanov, 2022-10-23:
@rtaylo congrats! Coincidentally, I just got a brand new baby as well! I'm hoping to get some time to work on a new project of mine during my paternity leave (stay tuned), though so far it's been pretty baby-centric, as expected.

rtaylo, 2022-10-24:
Congratulations to you as well!! Our little one just hit one month old
yesterday. Sleep is getting pretty hectic lol. Looking forward to see what
new projects you come up with!

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

rtaylo, 2022-10-26:
@nurglexp I was looking on Ali Express and someone seems to be selling a "new" version of the Sipeed microphone.
https://bit.ly/3FfLEH6
Ordered a few to test out, I'll report back

rtaylo, 2022-10-26:
Whoops sorry about that.
Try this:
https://www.aliexpress.us/item/3256804659411651.html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

nikivanov, 2022-10-26:
That looks like a drop in replacement. Please let me know how it goes and I
can update the BOM if all goes well. Thanks!

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

nurglexp, 2022-12-03:
@rtaylo any luck with the replacement microphone?

nikivanov, 2022-12-14:
I'm also very curious about this new version!

rtaylo, 2023-02-04:
@nurglexp the new microphone fixed the issue!

nurglexp, 2023-02-04:
Amazing, thanks for the confirmation. Ordered the replacement microphone 👯

nikivanov, 2023-02-04:
I'd recommend ordering a couple, especially if ordering from AliExpress -
quality control seems to be pretty poor with them. Glad this worked out!

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

Closed 2023-02-04.

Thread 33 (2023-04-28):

Issues with UPS communicating with Raspberry PI

EGimagination, 2023-04-28:
Hello, I'm having a single issue with Watneys UPS comms. In order to get it communicating/ running I had to change the address from 0x17 to 0x68 and the software works with one issue.
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
The battery reads 42% no matter the actual battery voltage is. It also does not sense when its charging making it hard to tell weather or not its going to survive the night haha.
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

I assume its something to do with the raspberry pi not communicating with the UPS? all the parts are identical to the BOM. Any help would be greatly appreciated!

Thanks,
Eric

nikivanov, 2023-04-29:
Hi Eric!

First of all, just wanted to say thank you for making a Watney for kids to learn 3D printing and get into STEM - that is truly heartwarming.

In terms of changing the address, I don't think this is correct. Per documentation, the address is indeed 0x17: https://wiki.52pi.com/index.php/EP-0136#USB_Plus_V5.0_Register_Mapping_Chart . 0x68 looks to be the RTC module, so you not getting the correct data is to be expected.

What error do you get when the address is 0x17? Are you absolutely sure you bought UPS-Plus (EP-0136) and not UPS (EP-0118) ?

nikivanov, 2023-04-29:
Additionally, see what results you get when you scan for available i2c devices: https://learn.adafruit.com/scanning-i2c-addresses/raspberry-pi

nerdymark, 2023-04-30:
My 0x17 is no longer visible. I think the board went bad, other addresses are visible. Maybe we're having the same problem. I'm looking for an alternative UPS solution because this will be my 2nd one to have failed.

EGimagination, 2023-04-30:
Thanks for the quick reply! Good catch on the model numbers the one I have is the EP-0118. I'm getting better results. If you have any advice on how to properly read the values with the powerplant.py portion of the code would be greatly appreciated!

This is the result from the I2C scan
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

I used some demo code to confirm that the device was communicating properly.
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

Then updated the powerplant.py address to 0x40 & this is what the battery portion is showing me.
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

nikivanov, 2023-05-01:
I'm afraid EP-0118 is simply not compatible with the features you're looking to enable: it only reads the voltage on the output of the 5V regulator, which is, unsurprisingly, 5V regardless of the state of charge of the batteries or the input voltage from the charger. Therefore, you won't be able to see the battery charge or the charging state unless you upgrade to EP-0136

nikivanov, 2023-05-01:
@nerdymark that's strange that they keep breaking on you. Did you flash the v10 firmware on your EP-0136?

nerdymark, 2023-05-02:
> @nerdymark that's strange that they keep breaking on you. Did you flash the v10 firmware on your EP-0136?

The first one I broke by doing something I shouldn't have done: un-mount it while batteries were installed. I bridged a connection and let out some magic smoke.
Second one I'm sure I broke too. It turns out my batteries were very dead, so I put different ones in it and ran the self-diag on it. The charger is not charging the batteries. I think I broke it by having the pi and the board both plugged into a USB-C power supply at the same time.
Third one is arriving today, lessons learned :)

nerdymark, 2023-05-02:
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
Mine's working again with the replacement upsplus.
ServoCity Runt Rover platform, a couple of hats with the motor controllers, speaker amps, etc

nikivanov, 2023-05-06:
@nerdymark so you're running the software on a different hardware chassis? Awesome! How's tank turning working with 3 wheels per side? Does your camera tilt up and down?

nerdymark, 2023-05-06:
> @nerdymark so you're running the software on a different hardware chassis? Awesome! How's tank turning working with 3 wheels per side? Does your camera tilt up and down?

It turns fine though I'm sure it could be better. The wheels are powered by the big battery in the back that can output 5 - 12v. I have 3 motor controllers sharing 9 volts from it. The camera tilts up and down.

The echo sensor is experimental, I had modified the motor controller to not move the rover if it's too close to something.

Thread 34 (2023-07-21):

Raspberry Pi Camera 3 incompatibility

camrichmond, 2023-07-21:
I recently started building a Watney, and I've run into an issue with the new official Raspberry Pi camera module V3. Unfortunately these new modules aren't compatible with Buster and raspivid - instead they require the new drivers from Bullseye and libcamera or Picamera2.

I've made some progress by upgrading the installed Watney image to Buster. I can now see my camera module with a vcgencmd get_camera, but there are some broken dependencies when trying to install libcamera-apps that I still need to resolve. Someone more savvy than me could probably make this change easily, but I might just make it easier on myself and buy an older wide-angle camera module. FWIW my old 1st generation camera module works perfectly right out of the box with the stock Watney image.

I just wanted to let anyone who might be running into the same issue know that the newer V3 cameras won't work with the current Watney image. Keep up the great work - this is a really fun project!

camrichmond, 2023-07-21:
Update - after resolving some dependencies and modifying the video.sh file to use libcamera-vid instead of raspivid, it works! Because libcamera was built to eschew the proprietary Broadcom GPU-reliant legacy apps, most of the options remain the same, but here are the updated contents of video.sh that work on Bullseye:

`libcamera-vid -n --width 1280 --height 720 --bitrate 2500000 --framerate 25 -t 0 --profile baseline --intra 25 --flush -o -| gst-launch-1.0 fdsrc do-timestamp=true ! h264parse ! rtph264pay config-interval=1 pt=96 ! udpsink host=127.0.0.1 port=8004`

Hopefully that's helpful to someone!

nikivanov, 2023-07-27:
Thanks @camrichmond! I'll make a note on the main page regarding this. How is the new camera module working for you? I found the non-fisheye cameras a bit too tough to drive with, since you're not seeing the environment right next to the rover.

Closed 2023-08-01.

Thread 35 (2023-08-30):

esp32 + esp32cam

eerison, 2023-08-30:
Hi @nikivanov

thank you  for the project, you did a nice project <3

I was wondering if you have any example using esp32 I guess it could reduce cost of the project.

and to make mic+speaker works, did you use i2s protocol or something else?

nikivanov, 2023-08-30:
@eerison The software stack runs on python / linux and relies on raspberry pi's hardware video encoding. ESP32 can do none of those things. It could be rewritten to use ESP32 / esp32cam, but the video quality and framerate would be drastically worse. Besides that, ESP32 most likely isnt powerful enough to encode and decode audio either. But to answer your other question - yes! Both microphone and the audio amp are using I2S - one uses the left channel, and the other uses the right one.

nikivanov, 2023-08-31:
I2S functionality resides exclusively on the raspberry pi device, the server. The browser simply gets an audio/video feed from the server. The technology behind it is WebRTC - same technology that's used for audio / video calls through the browser. The browser does not know where AV signals come from.

Here are some code links that set up the audio:

- [Here](https://github.com/nikivanov/watney/blob/master/packer/watney-image.json#L66) we disable the analog onboard audio of the raspberry pi
- [Here](https://github.com/nikivanov/watney/blob/master/packer/watney-image.json#L68) we add the googlevoicehat-soundcard overlay which is basically the driver for the microphone and the amp
- [Here](https://github.com/nikivanov/watney/blob/master/packer/watney-image.json#L69) is some i2s magic that does... something. If you google it, it might not be needed anymore :)
- [Here](https://github.com/nikivanov/watney/blob/master/packer/asound.conf) and [here](https://github.com/nikivanov/watney/blob/master/packer/asound.state) we set up the "soft volume" which allows us to control the volume of the amplifier in software via Alsa
- [Here](https://github.com/nikivanov/watney/blob/master/audiomanager.py#L15) is a snippet from the GStreamer pipeline that records audio from the mic - note the "channels=1" parameter. It might be easier to look at the [testrecord.sh](https://github.com/nikivanov/watney/blob/master/testrecord.sh) and [testplayback.sh](https://github.com/nikivanov/watney/blob/master/testplayback.sh) pipelines that are much simpler. The first one will record a file from the mic, the second will play it back.
- Lastly, note that in the [audio wiring diagram](https://github.com/nikivanov/watney/blob/master/images/wiring/audio%20wiring.png), the SD pin of the amplifier is connected to GPIO16, which is controlled by the googlevoicehat driver. When it's low, the amp is shut down. When it's high, per [this spec](https://learn.adafruit.com/adafruit-max98357-i2s-class-d-mono-amp/pinouts), `If the voltage on SD is higher than 1.4V then the output is the Left channel.` . Also observe that the microphone's LR pin is connected to the 3.3V pin of the raspberry pi, and it says on the [microphone itself](https://github.com/nikivanov/watney/blob/master/images/bom/microphone.jpg) LR=H (meaning High) - Right. So the amp uses the I2S left channel when doing playback, and the microphone is using the right channel for recording

Hope that helps!

nikivanov, 2023-08-31:
As for the camera, things are much simpler there - the server starts [this](https://github.com/nikivanov/watney/blob/master/video.sh) file when the WebRTC session is started. It acquires the hardware-encoded h264 video stream from the Pi, then adapts it to the RTSP (real time streaming protocol) and then pipes it to a local UDP port, where it gets picked up by the Janus WebRTC server.

In general, the pattern is to have Janus handle all WebRTC related stuff. Janus either pushes the audio bytes to a UDP socket, or reads bytes from a UDP socket to play back or record audio / video. The bytes are either picked up by GStreamer in case of playback, or pushed by the GStreamer to those UDP sockets in the case of recording

nikivanov, 2023-09-05:
@eerison I'm closing this issue since your questions have been answered. Feel free to reach out if you have any followups.

Closed 2023-09-05.

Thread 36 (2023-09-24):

Use Docker

eerison, 2023-09-24:
Hi @nikivanov

I was wondering... have you considered to use docker instead of packer? Why?

-  Because packer could be used just for few boards,
- And when you release a new image I must reinstall the SO,  and with docker I just need to pull the new image,  and In case there is some issue, I could revert easily.
- docker gonna work basically with all boards that uses Linux

nikivanov, 2023-09-25:
Hey @eerison!

The code uses pigpio which only works with raspberry pis from what I know, so making Watney more board-agnostic would involve more than just a docker image. Beyond that, I simply didn't see any advantage to using docker - it may not require extra compute, but it certainly wouldn't make the code more performant than running the process natively.

That being said, feel free to try it yourself and if it works, please open a PR and I can provide the docker image in addition to the native SD card image.

eerison, 2023-09-25:
I see,  I am not saying that docker gonna be more performing,  but the current image just works for raspberry...

Just to know,  do you have any suggestion , to make the project works for more boards? Like banana pi or orange pi

eerison, 2023-09-25:
> I see, I am not saying that docker gonna be more performing, but the current image just works for raspberry...
>
> Just to know, do you have any suggestion , to make the project works for more boards? Like banana pi or orange pigpio works only for raspberry? 😶‍🌫️

And why pi

eerison, 2023-09-25:
An regarding for pigpio , is it used just to integrate with pins, or is it used somewhere else?

Is it used in one place,  or many places in the code?

And do you think pigpio is the biggest impediment?

I was thinking to use armbian, maybe it could be an alternative to support different boards

nikivanov, 2023-09-25:
PIGPIO, raspivid, googlevoicehat-soundcard are all raspberry pi native, to name a few.

The board would also have to support hardware video encoding, I2C, SPI and I2S. OrangePi might support all that but it'd be a good amount of work to make Watney board-agnostic

Closed 2023-10-04.

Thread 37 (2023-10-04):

Use traefik as proxy

eerison, 2023-10-04:
Hey @nikivanov

after authenticate in the wifi, is it possible to change the password again?

eerison, 2023-10-04:
other question do you have any idea why it does not work access via proxy?

I am adding it in traffic but it is not working :/, any idea why? does it work with other host or just watney.local?

nikivanov, 2023-10-04:
If the password of the access point changes, Watney will no longer be able to connect to it. Whenever Watney boots up and cannot connect to any of its known networks, it restarts in AP mode as mentioned [here](https://github.com/nikivanov/watney#configuration)

As far as proxy access goes, watney.local may not work because mDNS resolution may not work through the proxy. You need to find Watney's IP as it is seen my your client computer that's connected to the proxy and use that IP instead of watney.local .  I use [Zerotier](https://github.com/nikivanov/watney#remote-access) for remote access of my Watneys and mDNS works just fine with it

eerison, 2023-10-04:
Ok cool, via ip it worked, I am just facing a issue related with janus, I guess I just need to add this port also

POST https://sub.mydomain.com:8089/janus net::ERR_CONNECTION_REFUSED

is there any way to access like

https://sub-janus.mydomain.com/janus instead of https://sub.mydomain.com:8089/janus ?

because I do not expose ports just 443

nikivanov, 2023-10-04:
That would be a question for Janus. I use zerotier because it takes care of
all the ports. I'm not sure how to set up Janus via a proxy.

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

eerison, 2023-10-05:
When you open watney via your proxy

Do you have a request for 8089/janus? If yes then you expose 8089 port right?

eerison, 2023-10-05:
Ok I found where it should be changed

https://github.com/nikivanov/watney/blob/master/js/watney_janus.js#L50

Is there anyway to get config variables in this file?

nikivanov, 2023-10-05:
I'm not sure what you're asking. You can modify this file as you see fit
locally. What config variables are you trying to get and in what context?

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

eerison, 2023-10-06:
> I'm not sure what you're asking. You can modify this file as you see fit locally. What config variables are you trying to get and in what context?
> […](#)
> On Thu, Oct 5, 2023, 2:12 AM Erison Silva ***@***.***> wrote: Ok I found where it should be changed https://github.com/nikivanov/watney/blob/master/js/watney_janus.js#L50 Is there anyway to get config variables in this file? — Reply to this email directly, view it on GitHub <[#37 (comment)](https://github.com/nikivanov/watney/issues/37#issuecomment-1748153898)>, or unsubscribe <https://github.com/notifications/unsubscribe-auth/AAJ45SHDK7PQEORKMAF7WRLX5ZFVLAVCNFSM6AAAAAA5TAVIM2VHI2DSMVQWIX3LMV43OSLTON2WKQ3PNVWWK3TUHMYTONBYGE2TGOBZHA> . You are receiving this because you were mentioned.Message ID: ***@***.***>

Ok I know that I could access the raspberry and change this file directly, and solve my issue.

But don't you think that others people gonna face the same issue later?

My idea is add [.env](https://www.npmjs.com/package/dotenv) in the project and get this host from there like

SERVER_HOST_JANUS=https://my.domain.com

If this env is set, then I use this host,  instead of the current one.

Does it make sense?

eerison, 2023-10-06:
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

I changed this line into the server, but the client keep doing request to the same host, the changes did not apply.
any idea why? is there any cache that I need to clean?

nikivanov, 2023-10-06:
No idea. With respect, you're not encountering an issue with Watney as it was designed to be used. You're trying to achieve an unsupported use case in this post and your other posts regarding other ARM boards, packer vs docker etc. You're welcome to try to figure it out yourself and if you get it to work, I'd be happy to merge it in, but I'm afraid I don't have time to help you add these new use cases.

eerison, 2023-10-06:
But I'm Testing with a raspberry pi 3b+ 😕

nikivanov, 2023-10-06:
Only raspberry pi 3a+ is supported, though my guess is that 3b+ should work as well. But this is a great example: if 3b+ ends up not working for you and you'd like to make it work, this wouldn't be an issue with Watney, as it's not designed for it. You're welcome to try to make it work with 3b+, but it would be on you to figure out how.

In general, I don't want to discourage you from trying to make Watney work outside of its supported use cases, but you keep opening issues with generic "how do I do X?" questions and the answer to all of them is "It's not supported. If you'd like it to be, you need to figure it out". I hope I'm not sounding rude - that's not the intention. It's just I've made all the improvements I wanted to this project and don't want to spend more time on it beyond supporting existing documented use cases.

eerison, 2023-10-28:
Hey @nikivanov

do you have any idea how this watney.local is configurated.
when I connect into my local network (via vpn), I can ping local ip, watney.lan, but I can not ping at watney.local.

maybe if I found this issue, maybe  I could find the solution why It is working just for audio/speaker, and not for video.

nikivanov, 2023-10-28:
watney.local is just mDNS. The raspberry pi image sets the hostname of the
device to watney which makes it accessible at watney.local

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

Closed 2023-10-06.

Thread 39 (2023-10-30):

Feature play audio

eerison, 2023-10-30:
Hey @nikivanov

I am adding a feature to play audio from sd card.

I am using the lib `mpg123 my-audio.mp3`,  could I add this lib into the project?
if yes I will provide a PR ;)

nikivanov, 2023-10-30:
You can add whatever libraries you want to your local project - you don't
need my permission to do so. If I were you I'd go with using gstreamer to
play the mp3 since it's already installed, but either would work.

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

eerison, 2023-10-30:
I know that I can do this just for my side, I was wondering if make sense I add this feature to play audio into your repository as a feature.

the idea is list the files from the folder in a dropdown( like the dropdown for choose output device).

does it make sense to include in your project?

nikivanov, 2023-10-30:
Sure, just please put it under a feature flag in the config, so it only shows up if it's enabled

eerison, 2023-11-04:
Hey Nikivanon, did you have any example for feature flag in JS?

because to enable/disable it I need to get it in `watney.js` file, but I did not see any example.

nikivanov, 2023-11-04:
No, currently the only feature flag is for the server side feature of off
charger re-docking.

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

eerison, 2023-11-04:
> No, currently the only feature flag is for the server side feature of off charger re-docking.
> […](#)
> On Sat, Nov 4, 2023, 8:27 AM Erison Silva ***@***.***> wrote: Hey Nikivanon, did you have any example for feature flag in JS? because to enable/disable it I need to get it in watney.js file, but I did not see any example. — Reply to this email directly, view it on GitHub <[#39 (comment)](https://github.com/nikivanov/watney/issues/39#issuecomment-1793430014)>, or unsubscribe <https://github.com/notifications/unsubscribe-auth/AAJ45SEPBLOBE6W5RFDF6CTYCYYEPAVCNFSM6AAAAAA6WAUHQ6VHI2DSMVQWIX3LMV43OSLTON2WKQ3PNVWWK3TUHMYTOOJTGQZTAMBRGQ> . You are receiving this because you were mentioned.Message ID: ***@***.***>

well as I need to add this feature behind a feature flag, and there isn't anything implemented for frontend, I will close this issue until find any solution for this ;)

Closed 2023-11-04.

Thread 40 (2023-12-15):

name 'AudioManager' is not defined

eerison, 2023-12-15:
Did you face this issue? note I am using the default image

```
Dec 15 22:20:03 watney python3[807]: Using TLS with keys in '/home/pi'
Dec 15 22:20:03 watney python3[807]: Traceback (most recent call last):
Dec 15 22:20:03 watney python3[807]:   File "/home/pi/watney/server.py", line 173, in <module>
Dec 15 22:20:03 watney python3[807]:     audioManager = AudioManager(config)
Dec 15 22:20:03 watney python3[807]: NameError: name 'AudioManager' is not defined
Dec 15 22:20:03 watney systemd[1]: watney.service: Main process exited, code=exited, status=1/FAILURE
Dec 15 22:20:03 watney systemd[1]: watney.service: Failed with result 'exit-code'.
Dec 15 22:20:04 watney systemd[1]: watney.service: Service RestartSec=1s expired, scheduling restart.
Dec 15 22:20:04 watney systemd[1]: watney.service: Scheduled restart job, restart counter is at 21.
Dec 15 22:20:04 watney systemd[1]: Stopped Watney Service.
Dec 15 22:20:04 watney systemd[1]: Started Watney Service.
```

nikivanov, 2023-12-18:
I'm not sure how you can be using the default Watney image and have an import error. Please go into `watney` folder, do `git status` and post the output

eerison, 2023-12-18:
Now I am getting this error:

```
Dec 18 20:57:36 watney systemd[1]: Started Watney Service.
Dec 18 20:57:38 watney python3[1358]: Using TLS with keys in '/home/pi'
Dec 18 20:57:38 watney python3[1358]: Use hardware SPI
Dec 18 20:57:38 watney python3[1358]: Traceback (most recent call last):
Dec 18 20:57:38 watney python3[1358]:   File "/home/pi/watney/server.py", line 184, in <module>
Dec 18 20:57:38 watney python3[1358]:     powerPlant = PowerPlant(config)
Dec 18 20:57:38 watney python3[1358]:   File "/home/pi/watney/powerplant.py", line 10, in __init__
Dec 18 20:57:38 watney python3[1358]:     self.bus.write_byte_data(DEVICE_ADDR, 17, cutoffVoltage & 0xFF)
Dec 18 20:57:38 watney python3[1358]: OSError: [Errno 121] Remote I/O error
Dec 18 20:57:38 watney systemd[1]: watney.service: Main process exited, code=exited, status=1/FAILURE
Dec 18 20:57:38 watney systemd[1]: watney.service: Failed with result 'exit-code'.
Dec 18 20:57:39 watney systemd[1]: watney.service: Service RestartSec=1s expired, scheduling restart.
Dec 18 20:57:39 watney systemd[1]: watney.service: Scheduled restart job, restart counter is at 84.
Dec 18 20:57:39 watney systemd[1]: Stopped Watney Service.
Dec 18 20:57:39 watney systemd[1]: Started Watney Service.
Dec 18 20:57:40 watney python3[1364]: Using TLS with keys in '/home/pi'
Dec 18 20:57:41 watney python3[1364]: Use hardware SPI
Dec 18 20:57:41 watney python3[1364]: Traceback (most recent call last):
Dec 18 20:57:41 watney python3[1364]:   File "/home/pi/watney/server.py", line 184, in <module>
Dec 18 20:57:41 watney python3[1364]:     powerPlant = PowerPlant(config)
Dec 18 20:57:41 watney python3[1364]:   File "/home/pi/watney/powerplant.py", line 10, in __init__
Dec 18 20:57:41 watney python3[1364]:     self.bus.write_byte_data(DEVICE_ADDR, 17, cutoffVoltage & 0xFF)
Dec 18 20:57:41 watney python3[1364]: OSError: [Errno 121] Remote I/O error
Dec 18 20:57:41 watney systemd[1]: watney.service: Main process exited, code=exited, status=1/FAILURE
Dec 18 20:57:41 watney systemd[1]: watney.service: Failed with result 'exit-code'.
Dec 18 20:57:42 watney systemd[1]: watney.service: Service RestartSec=1s expired, scheduling restart.
Dec 18 20:57:42 watney systemd[1]: watney.service: Scheduled restart job, restart counter is at 85.
Dec 18 20:57:42 watney systemd[1]: Stopped Watney Service.
Dec 18 20:57:42 watney systemd[1]: Started Watney Service.
Dec 18 20:57:43 watney python3[1371]: Using TLS with keys in '/home/pi'
Dec 18 20:57:43 watney python3[1371]: Use hardware SPI
Dec 18 20:57:43 watney python3[1371]: Traceback (most recent call last):
Dec 18 20:57:43 watney python3[1371]:   File "/home/pi/watney/server.py", line 184, in <module>
Dec 18 20:57:43 watney python3[1371]:     powerPlant = PowerPlant(config)
Dec 18 20:57:43 watney python3[1371]:   File "/home/pi/watney/powerplant.py", line 10, in __init__
Dec 18 20:57:43 watney python3[1371]:     self.bus.write_byte_data(DEVICE_ADDR, 17, cutoffVoltage & 0xFF)
Dec 18 20:57:43 watney python3[1371]: OSError: [Errno 121] Remote I/O error
Dec 18 20:57:43 watney systemd[1]: watney.service: Main process exited, code=exited, status=1/FAILURE
Dec 18 20:57:43 watney systemd[1]: watney.service: Failed with result 'exit-code'.
Dec 18 20:57:45 watney systemd[1]: watney.service: Service RestartSec=1s expired, scheduling restart.
Dec 18 20:57:45 watney systemd[1]: watney.service: Scheduled restart job, restart counter is at 86.
Dec 18 20:57:45 watney systemd[1]: Stopped Watney Service.
```

```
pi@watney:~/watney $ git status
On branch master
Your branch is up to date with 'origin/master'.

nothing to commit, working tree clean
pi@watney:~/watney $ ^C
pi@watney:~/watney $ git remote -v
origin	https://github.com/nikivanov/watney.git (fetch)
origin	https://github.com/nikivanov/watney.git (push)
pi@watney:~/watney $ git status
On branch master
Your branch is up to date with 'origin/master'.

nothing to commit, working tree clean
pi@watney:~/watney $ git branch
* master
```

Context:

Why it was working and now not anymore?

the battery uncharged completely, and when I charged again it was turn on and off all the time, then I realised that the issue was: raspberry and all things was trying to turn on and couldn't because it hasn't enough battery.

then I disconnected the raspberry and then I could charge the battery to 100%, but after this it doesn't work anymore :/.

Note: power button is not working too :(, maybe I should reset the UPS? if yes how 👀 ?

eerison, 2023-12-22:
Watney is alive again, thank you <3

Closed 2023-12-22.

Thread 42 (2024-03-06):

Raspberry don't BOOT

nicolasbeni41, 2024-03-06:
Hello mon raspberry pi 3a+ ne boot avec l'IMG fourni mais avec une distribution raspbian normale oui que faire ?

bennyp3333, 2024-04-13:
The same thing happened to me. Return/RMA your raspberry pi if possible otherwise replace the start*.elf, fixup*.dat and bootcode.bin on the sd card after flashing with the respective files from [rpi-firmware-master](https://github.com/raspberrypi/rpi-firmware). At least that worked for me, YMMV.
https://www.thingiverse.com/thing:6493508

ZehnderUMN, 2024-04-20:
My pi 3a+ was not booting either. Replacing the files worked

moaazsidat, 2024-07-15:
Ran into the same with pi 3a+, replacing the files hasn't worked

nikivanov, 2024-08-01:
I'm hoping to do a 2024 model refresh of Watney with a better power plant and latest linux, but I don't have a timeline for it. Latest linux particularly should solve this issue.

ZehnderUMN, 2024-08-01:
Ok thank you, I am looking forward to it!Alan ZehnderOn Jul 31, 2024, at 20:24, Nik Ivanov ***@***.***> wrote:
I'm hoping to do a 2024 model refresh of Watney with a better power plant and latest linux, but I don't have a timeline for it. Latest linux particularly should solve this issue.

—Reply to this email directly, view it on GitHub, or unsubscribe.You are receiving this because you commented.Message ID: ***@***.***>

neuro717, 2025-03-12:
I have exact same issue, image is not working.
Replaced files, obviously something else -is- happening, but won't connect to network.

Would be great to have a refresh on Watney. There's no other telepresence rover that's so accessible, easily affordable, and cool looking =)

 and here's what's been done to identify the boot issue:

1.	Tried the ‘usual’ way after wiring, by sticking in the Balena / Pi imager created 64gb SD card, no sound (following instructions in the video)
2.	Thought it might just be the wiring/batteries, plugged the whole Raspi 3A+ out, plugged into a regular power supply with GPIO pinned to speaker, no sound
3.	Speculated that it’s the GPIO the core cause, unplugged those, no sound. Decided to measure the voltage in, its working (0.9V/0.1-0.2A) consumption on boot (as expected)
4.	Thought the Raspi might not be working, used the same SD card, flashed Raspbian with the same macOS device using Balena – all working
5.	Everything else confirmed to be working, decided to plug it into the HDMI with keyboard – no graphics
6.	Decided to force HDMI output – no image on HDMI either, so I can’t troubleshoot what’s going on
7.	Later, tried if I can ‘rebuild’ the image on a raspi lite image 64 – and gave up after a while.

nikivanov, 2025-03-12:
I appreciate the kind words! I'm very close to releasing my new project, and my plan is to do a Watney refresh for bookworm after it. I'll ping this thread once I have a new version working.

neuro717, 2025-03-28:
@nikivanov : If it takes too much time and effort to build a complete image, why not give instructions so users can add all dependencies, install apps, and do our own configs to run it? I think many on the thread can follow that.

neuro717, 2025-03-28:
Alright, gave up. Lightyears behind what's needed to get this up and running. Will wait for your next release.

nikivanov, 2025-04-02:
Hi! I know a few of you are waiting for the new image of Watney. Here's why it's taking longer than I thought: I built Watney on buster, which is really old at this point. The new debian version, bookworm, has some changes to network setup, so I can't even SSH into Watney over wifi. I need to build a new image, but a lot of setup things need to be fixed.

It's not all bad though, there's this: https://github.com/RPi-Distro/pi-gen - this is a much more reputable way of building Pi OS images with customizations. So I need to port the customizations from the current build system to pi-gen so at least I can SSH into the OS.

neuro717, 2025-04-02:
Well, if there’s any granular work I can do to help, let me know.

When I tried building the watney image from zero (and didn’t get it all up and running, got stuck at getting the UI work (probably flask?) and control the motors), that took me a day and tons of claude help.

Appreciate what you’re putting into this.

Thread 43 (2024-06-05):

Can't connect while using bookworm branch

bennyp3333, 2024-06-05:
I have the watney rover working with the provided _watney.img_ release ([Build Here](https://www.thingiverse.com/thing:6493508)), but its a little flakey so I thought I'd try to upgrade to bookworm arm64 to see if it makes it more stable and just to tinker a bit.

But I can't get it to work. I've tried compiling the bookworm branch using the `packer-builder-arm` multiple times as well as manually execute everything in _watey-image.json_. Each time with the same results. The rover will boot up as expected but can't connect through https://my-ip:5000 or https://watney.local:5000. Browser just says **ERR_CONNECTION_RESET**.

I had the release image working so I don't think there's any hardware issues. And its connected to internet, other devices on the network can ping it and see ports 22, 53 and 5000 open. And there's nothing in the logs that seems concerning, er no obvious errors.

I can't seem to tell what is going wrong. Is there something simple I'm missing? Or other debug steps I can do or other logs to look at beyond janus.log?
Any help would be appreciated!

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

Netstat output
~~~
pi@watney:~ $ netstat -lntu
Active Internet connections (only servers)
Proto Recv-Q Send-Q Local Address           Foreign Address         State
tcp        0      0 127.0.0.1:5001          0.0.0.0:*               LISTEN
tcp        0      0 0.0.0.0:5000            0.0.0.0:*               LISTEN
tcp        0      0 0.0.0.0:53              0.0.0.0:*               LISTEN
tcp        0      0 0.0.0.0:22              0.0.0.0:*               LISTEN
tcp6       0      0 :::8188                 :::*                    LISTEN
tcp6       0      0 ::1:8888                :::*                    LISTEN
tcp6       0      0 ::1:5001                :::*                    LISTEN
tcp6       0      0 :::7088                 :::*                    LISTEN
tcp6       0      0 :::8089                 :::*                    LISTEN
tcp6       0      0 :::53                   :::*                    LISTEN
tcp6       0      0 :::22                   :::*                    LISTEN
udp        0      0 0.0.0.0:53              0.0.0.0:*                  
udp        0      0 0.0.0.0:67              0.0.0.0:*                  
udp        0      0 0.0.0.0:5353            0.0.0.0:*                  
udp        0      0 0.0.0.0:45034           0.0.0.0:*                  
udp6       0      0 :::53                   :::*                       
udp6       0      0 :::8004                 :::*                       
udp6       0      0 :::8005                 :::*                       
udp6       0      0 :::42111                :::*                       
udp6       0      0 :::5002                 :::*                       
udp6       0      0 :::5004                 :::*                       
udp6       0      0 :::5353                 :::*
~~~
server.py output
~~~
pi@watney:~ $ /usr/bin/python3 -u /home/pi/watney/server.py
Using TLS with keys in '/home/pi'
DEBUG:root:Use hardware SPI
Set powerplant cutoff voltage to 3200 mv
Servo starting...
Starting TTS...
Heartbeat starting...
Executing '/opt/janus/bin/janus -F /opt/janus/etc/janus/'
Logging to '/home/pi/watney/janus.log'
Saying 'Watney... Online'
~~~

janus.log
~~~
Janus version: 1203 (1.2.3)
Janus commit: 2a1db57ef737a272faa8fc433fce5266603a4737
Compiled on:  Wed  5 Jun 11:44:46 CDT 2024

Logger plugins folder: /opt/janus/lib/janus/loggers
[WARN]  Couldn't access logger plugins folder...
---------------------------------------------------
  Starting Meetecho Janus (WebRTC Server) v1.2.3
---------------------------------------------------

Checking command line arguments...
Debug/log level is 4
Debug/log timestamps are disabled
Debug/log colors are enabled
Adding 'vmnet' to the ICE ignore list...
Using 192.168.1.206 as local IP...
Token based authentication disabled
Initializing recorder code
Initializing ICE stuff (Full mode, ICE-TCP candidates disabled, half-trickle, IPv6 support disabled)
TURN REST API backend: (disabled)
^[[33m[WARN]^[[0m Janus is deployed on a private address (192.168.1.206) but you didn't specify any STUN server! Expect trouble if this is supposed to work over the intern>
Crypto: OpenSSL >= 1.1.0
Fingerprint of our certificate: AF:C9:D7:CD:2C:82:2D:CB:75:B6:F0:0B:00:5F:B6:93:87:A5:45:0D:F9:BC:BE:E7:91:9C:B8:39:B5:F9:FC:FD
^[[33m[WARN]^[[0m Data Channels support not compiled
Sessions watchdog started
Event handler plugins folder: /opt/janus/lib/janus/events
Joining Janus requests handler thread
Loading event handler plugin 'libjanus_wsevh.so'...
^[[33m[WARN]^[[0m WebSockets event handler disabled
Loading event handler plugin 'libjanus_sampleevh.so'...
JANUS SampleEventHandler plugin initialized!
Loading event handler plugin 'libjanus_gelfevh.so'...
^[[33m[WARN]^[[0m GELF event handler disabled (Janus API)
^[[35m[FATAL]^[[0m [events/janus_gelfevh.c:janus_gelfevh_init:375] GELF event handler not enabled/needed, giving up...
Plugins folder: /opt/janus/lib/janus/plugins
Loading plugin 'libjanus_textroom.so'...
^[[33m[WARN]^[[0m Data channels support not compiled, disabling TextRoom plugin
^[[33m[WARN]^[[0m The 'janus.plugin.textroom' plugin could not be initialized
Loading plugin 'libjanus_videoroom.so'...
JANUS VideoRoom plugin initialized!
Loading plugin 'libjanus_videocall.so'...
JANUS VideoCall plugin initialized!
Loading plugin 'libjanus_streaming.so'...
JANUS Streaming plugin initialized!
Loading plugin 'libjanus_audiobridge.so'...
^[[33m[WARN]^[[0m Denoising via RNNoise NOT supported
JANUS AudioBridge plugin initialized!
Loading plugin 'libjanus_nosip.so'...
JANUS NoSIP plugin initialized!
Loading plugin 'libjanus_sip.so'...
^[[33m[WARN]^[[0m sofia-sip logs are going to be redirected and they will not be shown in the process output
JANUS SIP plugin initialized!
Loading plugin 'libjanus_voicemail.so'...
^[[31m[ERR]^[[0m [janus.c:main:5746] The 'janus.plugin.voicemail' plugin was compiled against an older version of the API (19 < 105), skipping it: update it to enable it a>
Loading plugin 'libjanus_echotest.so'...
JANUS EchoTest plugin initialized!
Loading plugin 'libjanus_recordplay.so'...
JANUS Record&Play plugin initialized!
Transport plugins folder: /opt/janus/lib/janus/transports
Loading transport plugin 'libjanus_pfunix.so'...
^[[33m[WARN]^[[0m No Unix Sockets server started, giving up...
^[[33m[WARN]^[[0m The 'janus.transport.pfunix' plugin could not be initialized
Loading transport plugin 'libjanus_websockets.so'...
libwebsockets logging: 0
Websockets server started (port 8188)...
JANUS WebSockets transport plugin initialized!
Loading transport plugin 'libjanus_http.so'...
WebSockets thread started
HTTP transport timer started
HTTPS webserver started (port 8089, /janus path listener)...
Admin/monitor HTTP webserver started (port 7088, /admin path listener)...
JANUS REST (HTTP/HTTPS) transport plugin initialized!
~~~

nikivanov, 2024-08-01:
Hi. I created the bookworm branch for a prototype, but it's nowhere near completion. I'm hoping to do a 2024 model refresh of Watney with a better power plant and latest linux, but I don't have a timeline for it.

Closed 2024-08-01.

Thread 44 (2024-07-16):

Asking for watney login

moaazsidat, 2024-07-16:
I'm currently trying to boot watney after flashing the sd card, and it's stuck on the following step

```
watney login:
```

I didn't see any username / password for this, or maybe I'm just being stupid, how can this be configured?

moaazsidat, 2024-07-16:
```
Default SSH credentials for Watney are pi / watney5
```
sorry I can't read, it's right there

Closed 2024-07-16.

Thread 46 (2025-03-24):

Which wide angle camera is used?

hozdemir, 2025-03-24:
waveshare website has 3 different angle fisheye cameras compatible with raspberry pi. 160, 185 and 200 degrees
which one would be the best choice?

https://www.waveshare.com/product/raspberry-pi/cameras/5m-pixels/rpi-camera-m.htm

https://www.waveshare.com/product/raspberry-pi/cameras/5m-pixels/rpi-camera-i.htm

https://www.waveshare.com/product/raspberry-pi/cameras/5m-pixels/rpi-camera-g.htm

nikivanov, 2025-03-25:
It's gotta be 160. 185 and 200 are extreme fisheye that would show Watney's camera box due to the wide angle.

hozdemir, 2025-03-25:
Thank you for your response

Closed 2025-03-25.

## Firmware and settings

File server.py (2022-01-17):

from audiomanager import AudioManager
from offcharger import OffCharger
from powerplant import PowerPlant
from aiohttp import web
from motorcontroller import MotorController
from servocontroller import ServoController
from lightscontroller import LightsController
from heartbeat import Heartbeat
from subprocess import call
import os
import pigpio
from configparser import ConfigParser
from alsa import Alsa
import ssl
import sys
from externalrunner import ExternalProcess
import asyncio
from januseventhandler import JanusEventHandler
from tts import TTSSpeaker
from startupSequence import StartupSequenceController

routes = web.RouteTableDef()

motorController = None
servoController = None
heartbeat = None
signalingServer = None
alsa = None
tts = None
powerPlant = None
startupController = None
audioManager = None
audioManagerThread = None
janusEventHandler = None
offCharger = None

@routes.get("/")
async def getPageHTML(request):
    return web.FileResponse("index.html")


@routes.post("/sendCommand")
async def setCommand(request):
    commandObj = await request.json()
    newBearing = commandObj['bearing']
    newLook = commandObj['look']
    newSlow = commandObj['slow']

    if newBearing in MotorController.validBearings:
        motorController.setBearing(newBearing, newSlow)
    else:
        print("Invalid bearing {}".format(newBearing))
        return web.Response(status=400, text="Invalid")

    if newLook == 0:
        await servoController.lookStop()
    elif newLook == -1:
        await servoController.forward()
    elif newLook == 1:
        await servoController.backward()
    else:
        print("Invalid look at {}".format(newLook))
        return web.Response(status=400, text="Invalid")

    return web.Response(text="OK")


@routes.post("/shutDown")
async def shutDown(request):
    call("sudo halt", shell=True)

@routes.post("/restart")
async def restart(request):
    call("sudo reboot", shell=True)


@routes.post("/sendTTS")
async def sendTTS(request):
    ttsObj = await request.json()
    ttsString = ttsObj['str']
    tts.sayText(ttsString)
    return web.Response(text="OK")


@routes.post("/setVolume")
async def setVolume(request):
    volumeObj = await request.json()
    volume = int(volumeObj['volume'])
    alsa.setVolume(volume)
    return web.Response(text="OK")


@routes.post("/heartbeat")
async def onHeartbeat(request):
    stats = heartbeat.onHeartbeatReceived()
    return web.json_response(stats)

@routes.post("/lights")
async def onLights(request):
    lightsObj = await request.json()
    on = bool(lightsObj['on'])
    if on:
        lightsController.lightsOn()
    else:
        lightsController.lightsOff()
    return web.Response(text="OK")

async def onJanusEvent(request):
    try:
        eventObj = await request.json()
        janusEventHandler.handleEvent(eventObj)
    except Exception as e:
        print('Error handling janus event: {}'.format(e))
    finally:
        return web.Response(text="OK")

# Python 3.7 is overly wordy about self-signed certificates, so we'll suppress the error here
def loopExceptionHandler(loop, context):
    exception = context.get('exception')
    if isinstance(exception, ssl.SSLError) and exception.reason == 'SSLV3_ALERT_CERTIFICATE_UNKNOWN':
        pass
    else:
        loop.default_exception_handler(context)


def createSSLContext(homePath):
    # Create an SSL context to be used by the websocket server
    print('Using TLS with keys in {!r}'.format(homePath))
    chain_pem = os.path.join(homePath, 'cert.pem')
    key_pem = os.path.join(homePath, 'key.pem')
    sslctx = ssl.create_default_context()

    try:
        sslctx.load_cert_chain(chain_pem, keyfile=key_pem)
    except FileNotFoundError:
        print("Certificates not found, did you run generate_cert.sh?")
        sys.exit(1)
    # FIXME
    sslctx.check_hostname = False
    sslctx.verify_mode = ssl.CERT_NONE
    return sslctx

runners = []
async def start_site(app, address, port, sslContext=None):
    runner = web.AppRunner(app)
    runners.append(runner)
    await runner.setup()

    if sslContext is not None:
        site = web.TCPSite(runner, host=address, port=port, ssl_context=sslContext)
    else:
        site = web.TCPSite(runner, host=address, port=port)
    await site.start()


if __name__ == "__main__":
    homePath = os.path.dirname(os.path.abspath(__file__))
    sslctx = createSSLContext(os.path.dirname(homePath))

    gpio = pigpio.pi()
    if not gpio.connected:
        print('GPIO not connected')
        exit()
    
    config = ConfigParser()
    config.read(os.path.join(homePath, "rover.conf"))
    audioConfig = config["AUDIO"]
    videoConfig = config["VIDEO"]

    loop = asyncio.get_event_loop()
    loop.set_exception_handler(loopExceptionHandler)

    audioManager = AudioManager(config)

    motorController = MotorController(config, gpio, audioManager)

    alsa = Alsa(gpio, config)

    servoController = ServoController(gpio, config, audioManager)
    lightsController = LightsController(gpio, config)

    tts = TTSSpeaker(config, alsa, audioManager)

    powerPlant = PowerPlant(config)

    startupController = StartupSequenceController(config, servoController, lightsController, tts)

    heartbeat = Heartbeat(config, servoController, motorController, alsa, lightsController, powerPlant)

    offCharger = OffCharger(config, tts, motorController)

    janus = ExternalProcess(videoConfig["JanusStartCommand"], False, False, "janus.log")
    videoStream = ExternalProcess(videoConfig["GStreamerStartCommand"], True, False, "video.log")

    janusEventHandler = JanusEventHandler()

    mainApp = web.Application()
    mainApp.add_routes(routes)
    mainApp.router.add_static('/js/', path=os.path.join(homePath, 'js'))
    loop.create_task(start_site(mainApp, '0.0.0.0', 5000, sslctx))

    eventListenerApp = web.Application()
    eventListenerApp.add_routes([web.post('/janusEvent', onJanusEvent)])
    loop.create_task(start_site(eventListenerApp, 'localhost', 5001))

    try:
        loop.run_forever()
    except:
        pass
    finally:
        servoController.stop()
        lightsController.stop()
        gpio.stop()
        janus.endProcess()
        videoStream.endProcess()
        for runner in runners:
            loop.run_until_complete(runner.cleanup())

    

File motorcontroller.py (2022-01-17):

from events import Events
from motor import Motor
import pigpio


class MotorController:
    validBearings = ["n", "ne", "e", "se", "s", "sw", "w", "nw", "0"]

    def __init__(self, config, gpio, audioManager):
        driverConfig = config["DRIVER"]
        leftMotorConfig = config["LEFTMOTOR"]
        rightMotorConfig = config["RIGHTMOTOR"]
        
        self.trim = float(driverConfig["Trim"])
        self.pwmFrequency = int(driverConfig["PWMFrequency"])

        leftMotor = Motor(
            gpio,
            self.pwmFrequency,
            int(leftMotorConfig["ForwardPin"]),
            int(leftMotorConfig["ReversePin"]),
            1 if self.trim >= 0 else 1 + self.trim,
            'Left Motor'
        )

        rightMotor = Motor(
            gpio,
            self.pwmFrequency,
            int(rightMotorConfig["ForwardPin"]),
            int(rightMotorConfig["ReversePin"]),
            1 if self.trim <= 0 else 1 - self.trim,
            'Right Motor'
        )

        self.leftMotor = leftMotor
        self.rightMotor = rightMotor

        self.gpio = gpio

        self.straightaway = float(driverConfig["Straightaway"])
        self.straightawaySlow = float(driverConfig["StraightawaySlow"])
        self.halfTurnUndersteer = float(driverConfig["HalfTurnUndersteer"])
        self.halfTurnSlowFactor = float(driverConfig["HalfTurnSlowFactor"])
        self.tankTurnSpeed = float(driverConfig["TankTurnSpeed"])
        self.tankTurnSpeedSlow = float(driverConfig["TankTurnSpeedSlow"])
        
        self.enablePin = int(driverConfig["EnablePin"])

        self.gpio.set_mode(self.enablePin, pigpio.OUTPUT)
        self.gpio.write(self.enablePin, pigpio.LOW)

        self.audioManager = audioManager
        self.audioToken = 'fe7a1846-a0bb-4a44-aa3e-5b080089d37a'

    def getTargetMotorDCs(self, targetBearing, slow):
        if targetBearing == "0":
            leftDC = 0
            rightDC = 0
        elif targetBearing == "n":
            if not slow:
                leftDC = 100 * self.straightaway
                rightDC = 100 * self.straightaway
            else:
                leftDC = 100 * self.straightawaySlow
                rightDC = 100 * self.straightawaySlow
        elif targetBearing == "ne":
            if not slow:
                leftDC = 100
                rightDC = 100 * self.halfTurnUndersteer
            else:
                leftDC = 100 * self.halfTurnSlowFactor
                rightDC = 100 * self.halfTurnUndersteer * self.halfTurnSlowFactor
        elif targetBearing == "e":
            if not slow:
                leftDC = 100 * self.tankTurnSpeed
                rightDC = -100 * self.tankTurnSpeed
            else:
                leftDC = 100 * self.tankTurnSpeedSlow
                rightDC = -100 * self.tankTurnSpeedSlow
        elif targetBearing == "se":
            if not slow:
                leftDC = -100
                rightDC = -100 * self.halfTurnUndersteer
            else:
                leftDC = -100 * self.halfTurnSlowFactor
                rightDC = -100 * self.halfTurnUndersteer * self.halfTurnSlowFactor
        elif targetBearing == "s":
            if not slow:
                leftDC = -100 * self.straightaway
                rightDC = -100 * self.straightaway
            else:
                leftDC = -100 * self.straightawaySlow
                rightDC = -100 * self.straightawaySlow
        elif targetBearing == "sw":
            if not slow:
                leftDC = -100 * self.halfTurnUndersteer
                rightDC = -100  
            else:
                leftDC = -100 * self.halfTurnUndersteer * self.halfTurnSlowFactor
                rightDC = -100 * self.halfTurnSlowFactor
        elif targetBearing == "w":
            if not slow:
                leftDC = -100 * self.tankTurnSpeed
                rightDC = 100 * self.tankTurnSpeed
            else:
                leftDC = -100 * self.tankTurnSpeedSlow
                rightDC = 100 * self.tankTurnSpeedSlow
        elif targetBearing == "nw":
            if not slow:
                leftDC = 100 * self.halfTurnUndersteer
                rightDC = 100
            else:
                leftDC = 100 * self.halfTurnUndersteer * self.halfTurnSlowFactor
                rightDC = 100 * self.halfTurnSlowFactor
        else:
            raise Exception("Bad bearing: " + targetBearing)

        return int(leftDC), int(rightDC)

    def setBearing(self, bearing, slow):
        if bearing not in self.validBearings:
            raise ValueError("Invalid bearing: {}".format(bearing))

        leftDC, rightDC = self.getTargetMotorDCs(bearing, slow)
        leftActive = self.leftMotor.setMotion(leftDC)
        rightActive = self.rightMotor.setMotion(rightDC)
        if leftActive or rightActive:
            self.gpio.write(self.enablePin, pigpio.HIGH)
            self.audioManager.lowerVolume(self.audioToken)
            Events.getInstance().fireMotionOn()
        else:
            self.gpio.write(self.enablePin, pigpio.LOW)
            self.audioManager.restoreVolume(self.audioToken)
            Events.getInstance().fireMotionOff()

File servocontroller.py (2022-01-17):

import asyncio
import time

class ServoController:

    def __init__(self, gpio, config, audioManager):
        servoConfig = config["SERVO"]
        self.pwmPin = int(servoConfig["PWMPin"])
        self.neutral = int(servoConfig["Neutral"])
        self.min = int(servoConfig["Min"])
        self.max = int(servoConfig["Max"])

        self.audioManager = audioManager
        self.audioToken = "927dff95-b82b-433c-885c-6ac9ac13d8b0"

        self.gpio = gpio

        self.changeVelocityPerSec = 1000
        # 1 is forward, -1 is backward, 0 is stop
        self.direction = 0
        self.timingLock = asyncio.Condition()
        self.task = None
        self.startLoop()

    async def forward(self):
        async with self.timingLock:
            self.direction = 1
            self.timingLock.notify()

    async def backward(self):
        async with self.timingLock:
            self.direction = -1
            self.timingLock.notify()

    async def lookStop(self):
        async with self.timingLock:
            if self.direction != 0:
                self.direction = 0
                self.timingLock.notify()

    def startLoop(self):
        loop = asyncio.get_event_loop()
        self.task = loop.create_task(self.timingLoop())

    async def timingLoop(self):
        print("Servo starting...")
        try:
            currentPosition = self.neutral
            lastChangeTime = None
            while True:
                async with self.timingLock:
                    if not self.__shouldBeMoving(currentPosition):
                        self.stopServo()
                        self.audioManager.restoreVolume(self.audioToken)
                        lastChangeTime = None
                        await self.timingLock.wait()

                self.audioManager.lowerVolume(self.audioToken)
                if not lastChangeTime:
                    changeDelta = 0
                else:
                    timeDelta = time.time() - lastChangeTime
                    changeDelta = self.changeVelocityPerSec * timeDelta

                lastChangeTime = time.time()

                if self.direction == 1:
                    currentPosition = max(currentPosition - changeDelta, self.min)
                elif self.direction == -1:
                    currentPosition = min(currentPosition + changeDelta, self.max)

                self.changeServo(currentPosition)
                await asyncio.sleep(0.05)
        except asyncio.CancelledError:
            self.stopServo()
            print("Servo stopped")
        except Exception as e:
            print("Unexpected exception in servo: " + str(e))

    def __shouldBeMoving(self, currentPosition):
        if self.direction == 0:
            return False
        elif self.direction == 1 and currentPosition <= self.min:
            return False
        elif self.direction == -1 and currentPosition >= self.max:
            return False

        return True

    def stopServo(self):
        self.gpio.set_servo_pulsewidth(self.pwmPin, 0)

    def changeServo(self, val):
        self.gpio.set_servo_pulsewidth(self.pwmPin, val)

    def stop(self):
        self.stopServo()

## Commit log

2017-12-28 switched to using rws
2018-02-19 Added sample video
2018-02-21 Removed debug print statements
2018-03-20 New tires, caster and cameras
    [articulator.stl, camera body - fisheye.stl, camera body - regular.stl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]
2018-04-17 servo control first checkin
2018-04-18 Changed servo frequency and resolution
2018-04-23 Switched to pigpio, turned down bitrate
2018-06-26 fixed rover current dir. added service def
2018-06-26 info button, shut down button, jquery ui
2018-06-27 Watney4 STL files
    [Camera mount.stl, Rover cover.stl, articulator.stl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]
2018-07-05 Updated stls and readme
    [bottom.stl, tire.stl]
2018-07-06 new stls
    [bottom.stl, camera body.stl, camera bucket.stl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]
2018-09-23 Watney 4D STLs
    [bottom.stl, camera body.stl, camera bucket.stl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]
2018-09-23 servo startup changed
2018-09-24 Assembly image fix
2019-01-18 mic button added
2019-04-03 Added signaling, everything is broken
    [alsa.py, server.py, servocontroller.py]
2019-04-04 servo is async. everything is still broken
    [events.py, server.py, servocontroller.py]
2019-04-05 fixed up async stuff. Mostly working
    [alsa.py, externalrunner.py, heartbeat.py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]
2019-04-05 servo works but wonky
2019-04-05 servo is ok
2019-05-27 added boot config, removed servo jitter while moving
    [config.txt]
2019-09-01 servo amplitude
2019-09-02 added bom
2019-09-02 started on bom
2019-09-02 bom modified
2019-09-07 fixed bom and slow
2019-09-20 added servo range
2019-09-20 updated bom
2019-09-20 added assembly
2019-09-20 more assembly
2019-09-25 fixed servo config
2019-09-25 added restart button
2019-10-07 finished assembly writeup
2019-10-08 finished assembly write up. Added slow info
2019-10-13 readme and assembly
2019-10-14 stls and readme
    [Charge client holder.stl, audio bonnet.stl, bottom.stl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]
2019-10-14 pwm notes
2019-10-14 added note about charging
2019-11-05 added dock stl
    [dock.stl]
2019-12-27 bad board
2019-12-27 added noted about the board
2020-11-29 switched to pigpio
2020-11-30 verified servo works with pigpio
2020-12-18 packer progress
    [config.txt]
2020-12-20 fixed servo and packer perms
    [server.py, servocontroller.py]
2020-12-20 changed servo pin and fixed packer
2020-12-27 added power reading
2020-12-27 power reading plumbed through but not working
    [alsa.py, heartbeat.py]
2021-01-09 removed joystick code and power metering
2021-01-13 fixed recording device, mute and tts
    [tts.py]
2021-01-30 added battery voltage monitoring
2021-01-31 battery percentage
    [config.txt]
2021-02-03 try catching adc reading
2021-04-19 removed old battery monitor
2021-04-19 added powerplant
2021-05-02 added cutoff voltage
2021-05-02 changed charging indicator
2021-07-23 powerplant manually sets voltage limits
2021-08-09 feat: reverted powerplant top voltage
    [powerplant.py]
2021-08-19 higher pwm frequency config
2021-09-01 rewrote motor parameters and drive
2021-09-02 fixed initial volume set
    [heartbeat.py]
2021-09-10 more BOM updates
2021-09-10 bom dot com
2021-09-30 fixed delayed unmute logic
    [audiomanager.py]
2021-09-30 cleanup and fixed bom
2021-10-31 changed powerplant error reporting
    [powerplant.py]
2021-12-25 fixed readme and enabled checking
    [offcharger.py]
2022-01-15 changed cutoff voltage to 3200
2022-01-17 added wiring, videos and step
2022-07-14 mg90s servo, default pin settings
    [Camera bucket mg90s.stl, servo gear mg90s.stl]
2023-07-27 updated README with regards to camera module v3
2023-08-01 added v3 camera module link
